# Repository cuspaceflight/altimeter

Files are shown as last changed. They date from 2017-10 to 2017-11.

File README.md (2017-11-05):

# CUSF Altimeter
### This project is a barebones altimeter for use in the freshers rocket challenge. The below instructions are specific to Linux systems only.

## Setting up the Repositiory

1. Setup the repository using the following commands:
```
$ git clone https://github.com/cuspaceflight/altimeter.git
$ cd altimeter
$ git submodule update --init
$ cd ChibiOS
$ git checkout stable_16.1.x
```
2. To succesfully compile firmware you will need to install gcc:
```
$ sudo apt-get install gcc-arm-none-eabi
```
3. Test the installation by compiling the firmware template:
```
$ cd ../firmware
$ make
```

## Analysing Log Files

1. Copy the file "log_0000x.bin" you wish to decode into the altimeter/logs directory

2. From the terminal run:
```
$ python3 log_file_parser.py log_0000x.bin
```

The output will print directly to the terminal window.

## Making Firmware Changes

This will be explained in depth in the sessions, however the files which you will want to modify (status.c, measurements.c and logging.c) can be found in the altimeter/firmware directory.

Compile using the command:
``` 
$ make
```
If successful something similar to the below should appear in the terminal window:

```
...
Compiling testbmk.c
Compiling main.c
Compiling ms5611.c
Compiling measure.c
Compiling status.c
Compiling microsd.c
Compiling logging.c
Linking build/altimeter.elf
Creating build/altimeter.bin
Creating build/altimeter.hex
Creating build/altimeter.dmp
Creating build/altimeter.list

   text	   data	    bss	    dec	    hex	filename
  43900	   8896	 122628	 175424	  2ad40	build/altimeter.elf

Done
```

### References

ChibiOs - http://www.chibios.org/dokuwiki/doku.php?id=chibios:documentation:start

GDB - https://github.com/blacksphere/blackmagic/wiki/Useful-GDB-commands

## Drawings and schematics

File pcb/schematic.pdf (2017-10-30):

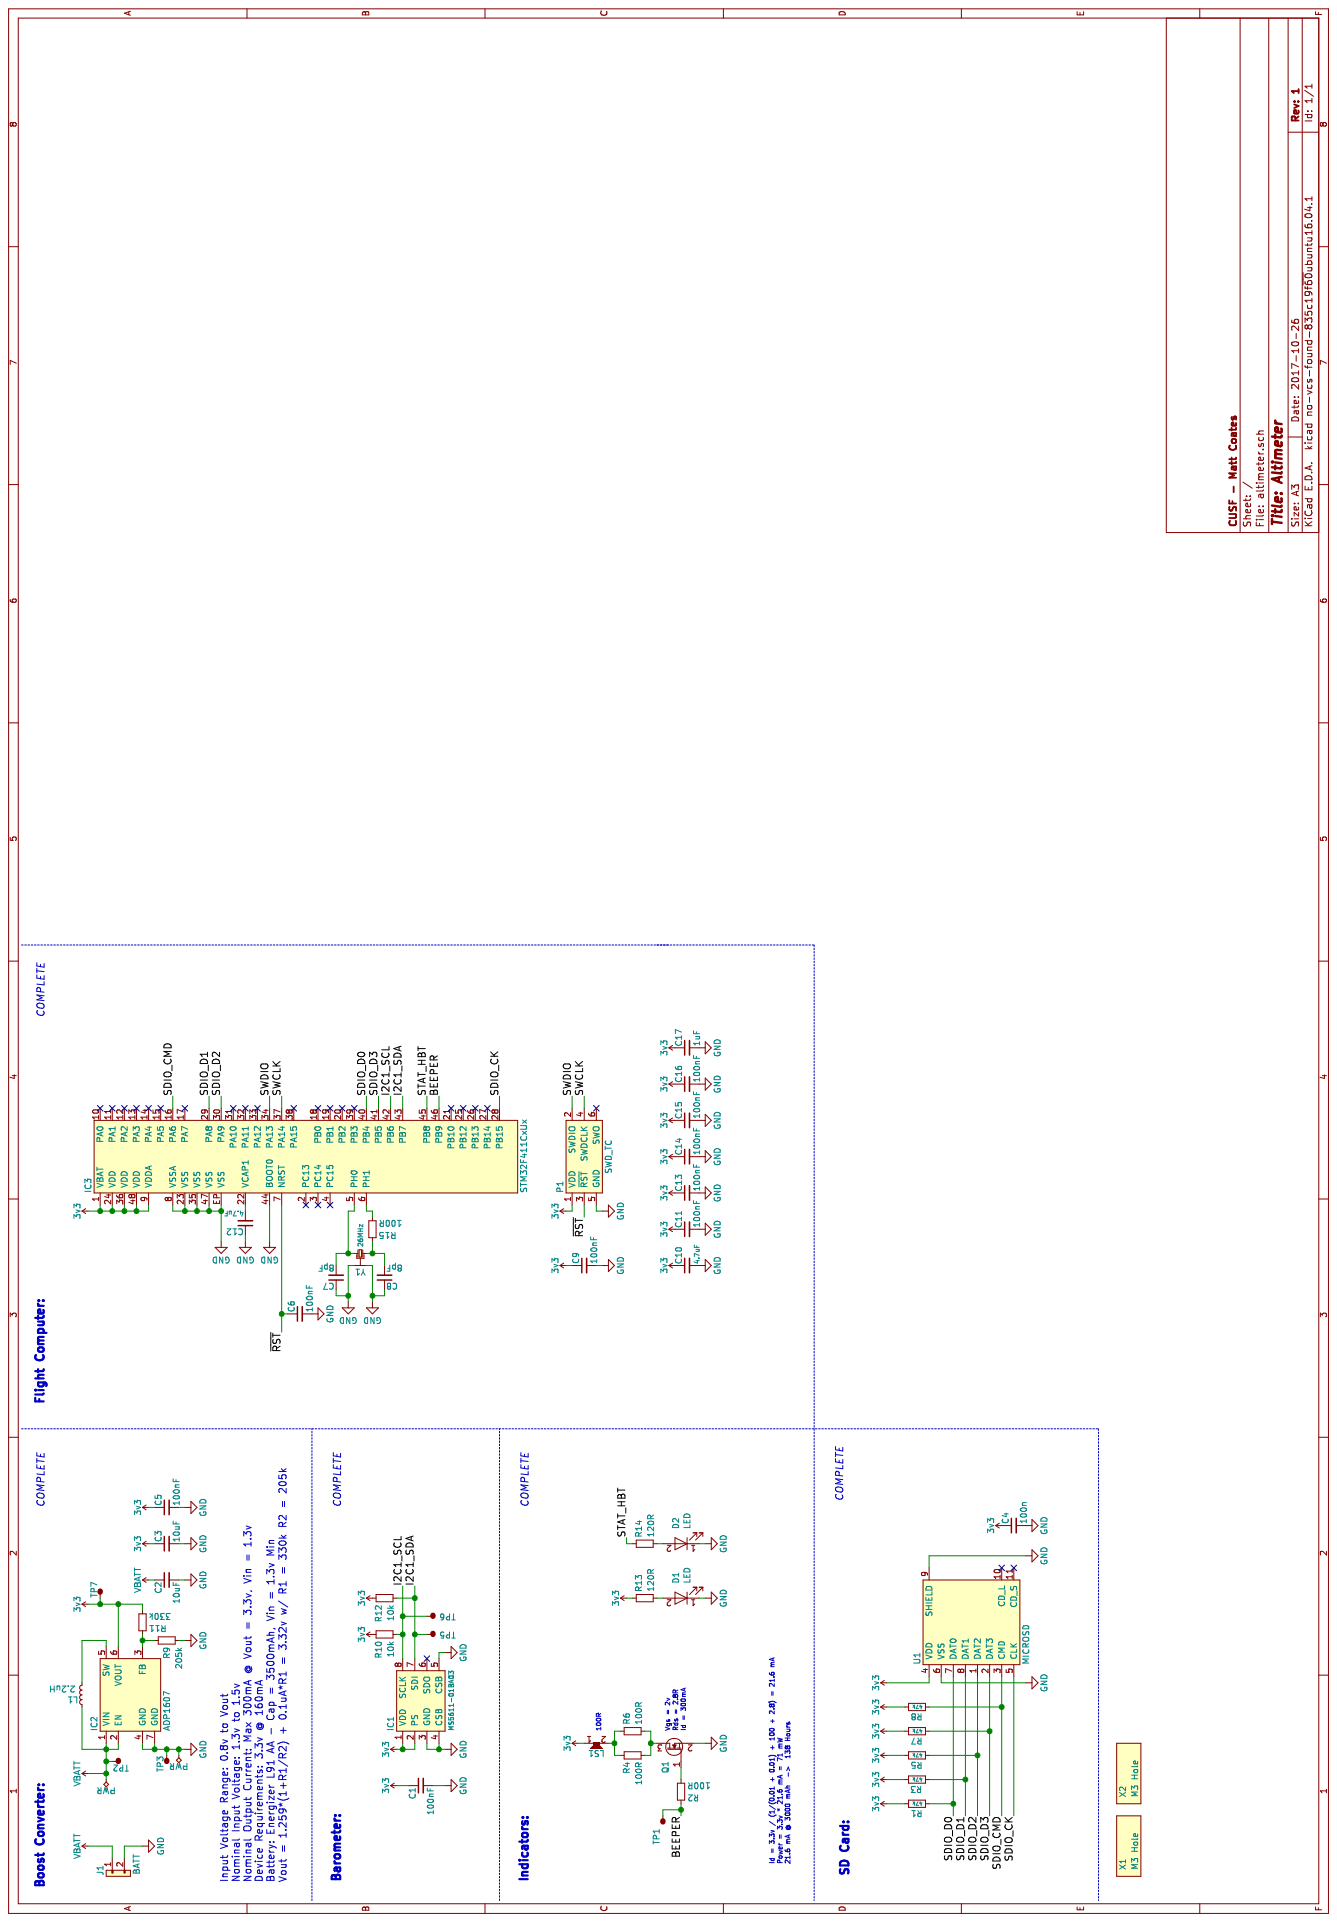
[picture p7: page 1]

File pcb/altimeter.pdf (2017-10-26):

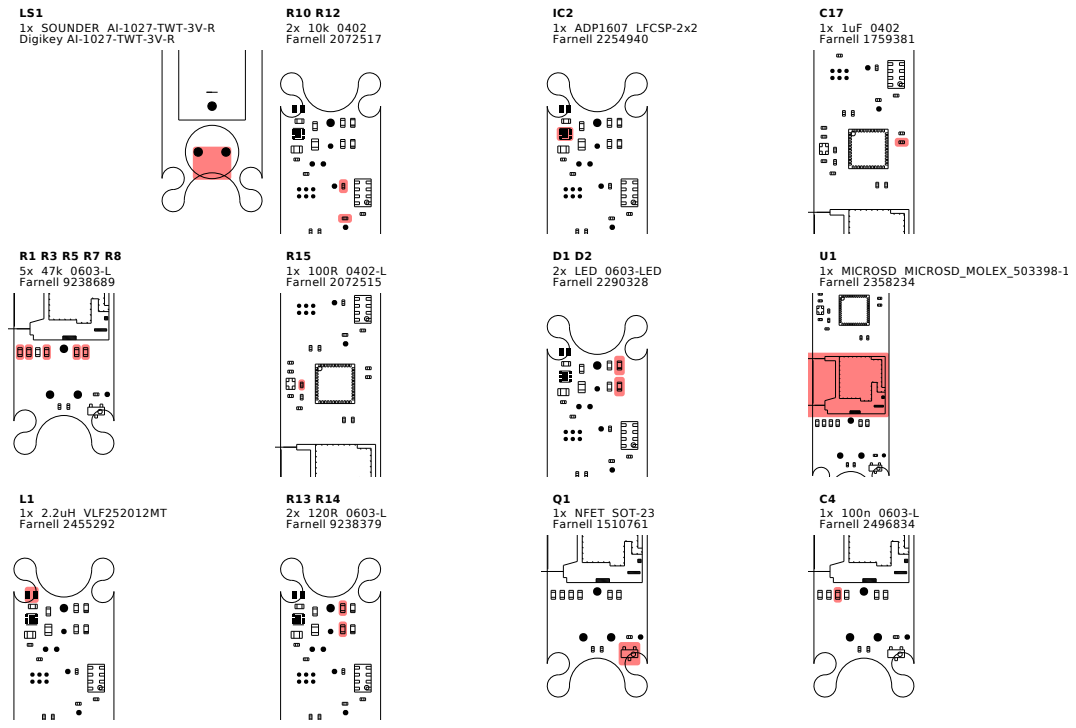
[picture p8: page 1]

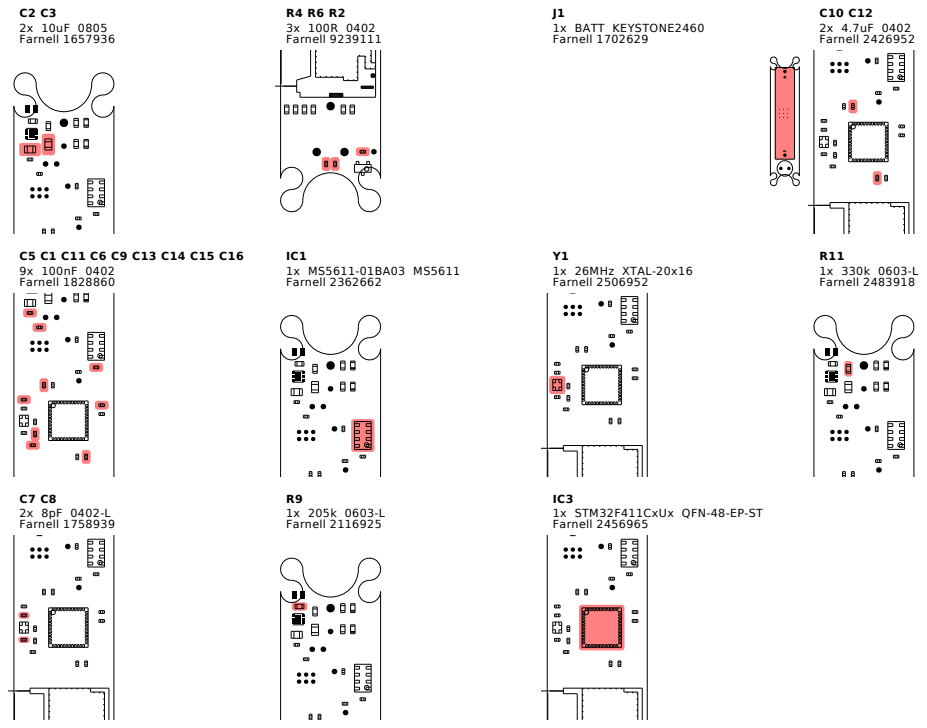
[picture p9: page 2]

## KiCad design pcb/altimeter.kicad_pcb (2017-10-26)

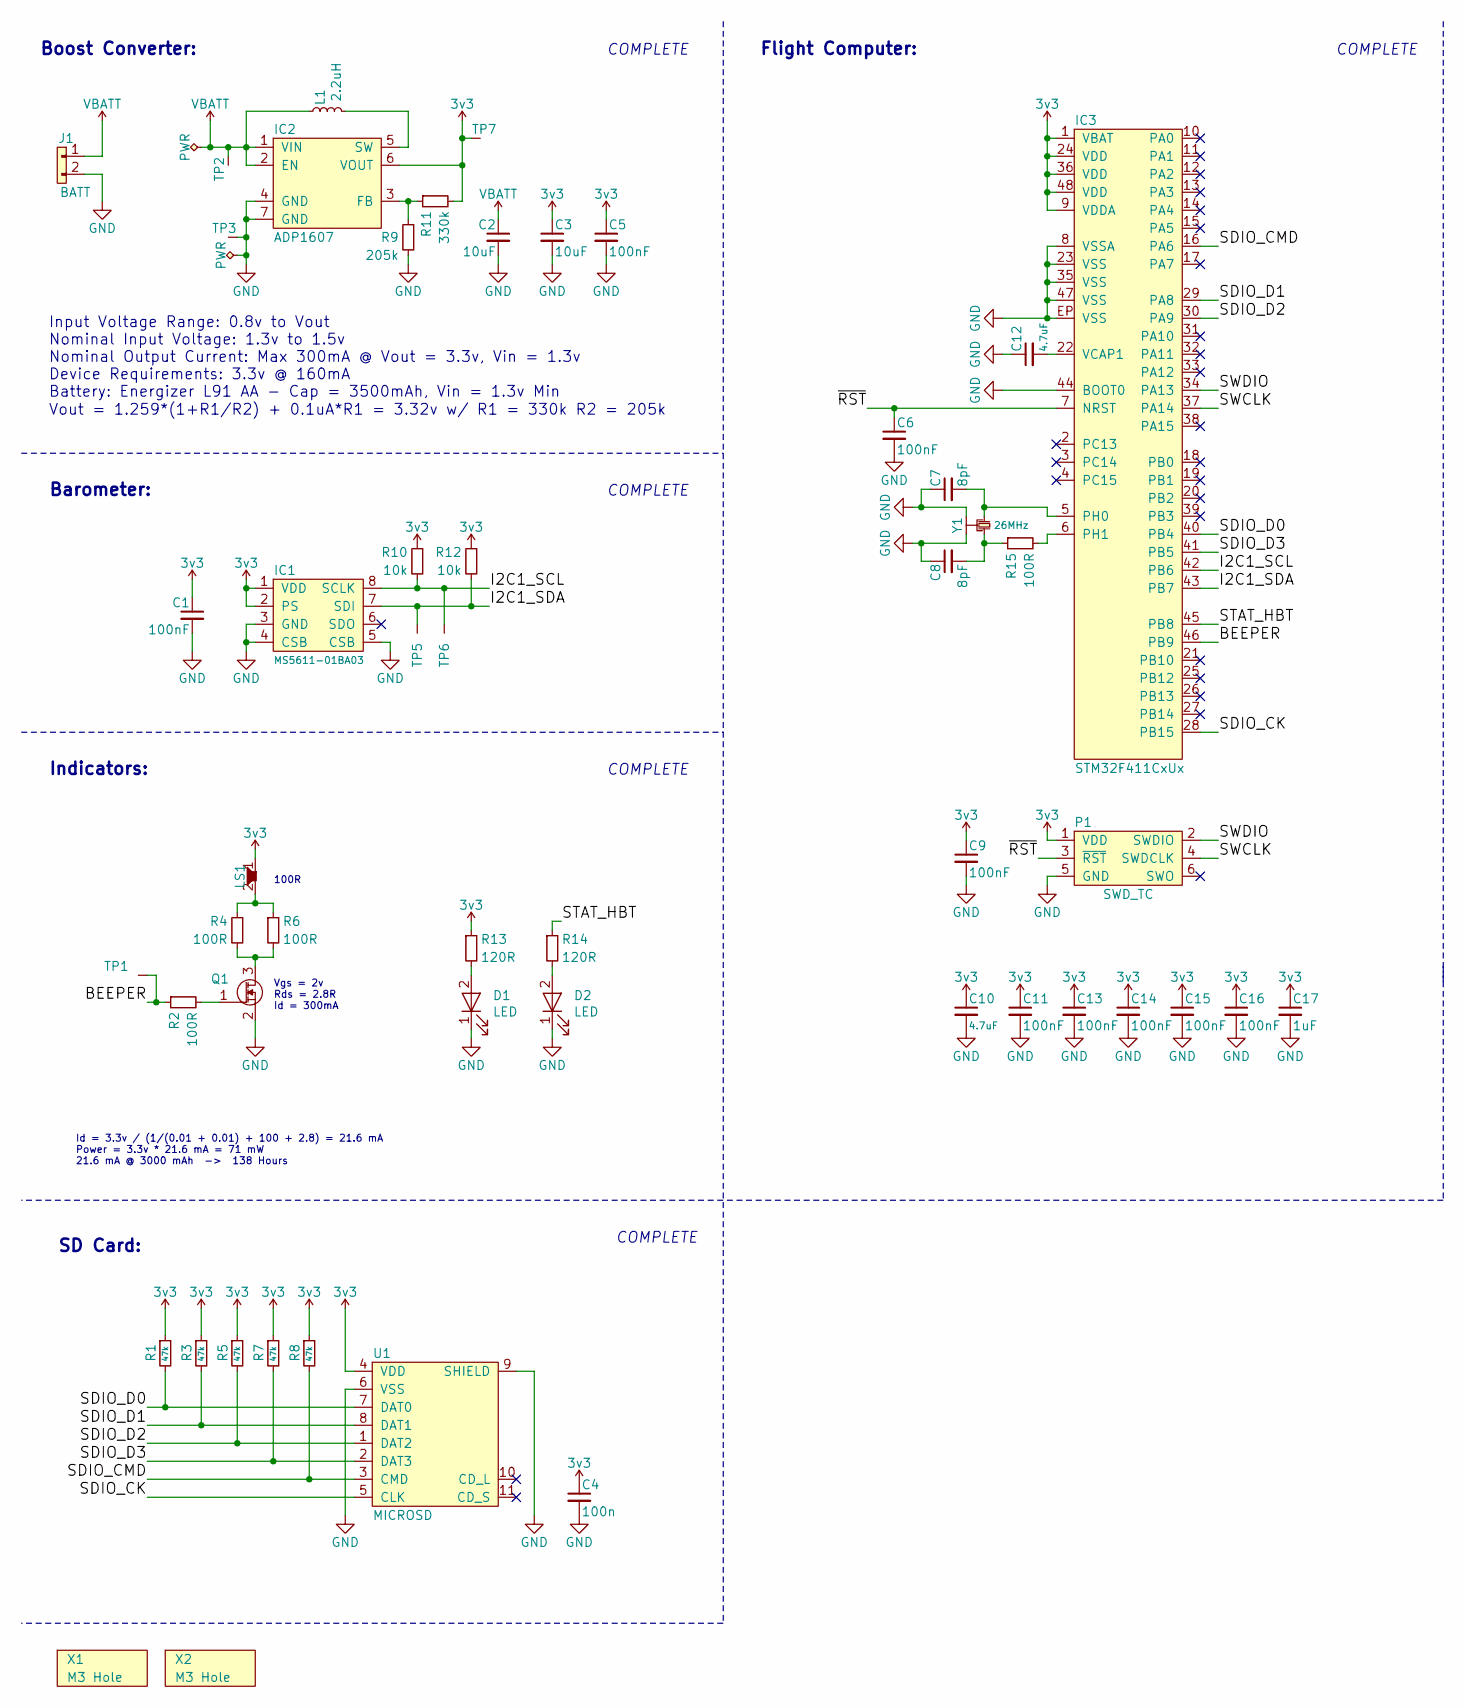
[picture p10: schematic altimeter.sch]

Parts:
C1, C5, C6, C9, C11, C13, C14, C15, C16: 100nF; 0402; Farnell 1828860
C2, C3: 10uF; 0805; Farnell 1657936
C4: 100n; 0603-L; Farnell 2496834
C7, C8: 8pF; 0402-L; Farnell 1758939
C10, C12: 4.7uF; 0402; Farnell 2426952
C17: 1uF; 0402; Farnell 1759381
D1, D2: LED; 0603-LED; Farnell 2290328
IC1: MS5611-01BA03; MS5611; Farnell 2362662
IC2: ADP1607; LFCSP-2x2; Farnell 2254940
IC3: STM32F411CxUx; QFN-48-EP-ST; Farnell 2456965
J1: BATT; KEYSTONE2460; Farnell 1702629
L1: 2.2uH; VLF252012MT; Farnell 2455292
LS1: SOUNDER; AI-1027-TWT-3V-R; Digikey AI-1027-TWT-3V-R
P1: SWD_TC; TC2030-NL
Q1: NFET; SOT-23; Farnell 1510761
R1, R3, R5, R7, R8: 47k; 0603-L; Farnell 9238689
R2, R4, R6: 100R; 0402; Farnell 9239111
R9: 205k; 0603-L; Farnell 2116925
R10, R12: 10k; 0402; Farnell 2072517
R11: 330k; 0603-L; Farnell 2483918
R13, R14: 120R; 0603-L; Farnell 9238379
R15: 100R; 0402-L; Farnell 2072515
TP1, TP2, TP3, TP5, TP6, TP7: TESTPAD
U1: MICROSD; MICROSD_MOLEX_503398-1892; Farnell 2358234
X1, X2: M3 Hole; M3_MOUNT
Y1: 26MHz; XTAL-20x16; Farnell 2506952

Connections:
3v3: C1.1, C3.1, C4.1, C5.1, C9.1, C10.1, C11.1, C13.1, C14.1, C15.1, C16.1, C17.1, IC1.1 (VDD), IC1.2 (PS), IC2.6 (VOUT), IC3.1 (VBAT), IC3.9 (VDDA), IC3.24 (VDD), IC3.36 (VDD), IC3.48 (VDD), LS1.1, P1.1 (VDD), R1.1, R3.1, R5.1, R7.1, R8.1, R10.1, R11.2, R12.1, R13.1, TP7.1, U1.4 (VDD)
/BEEPER: IC3.46 (PB9), R2.1, TP1.1
/I2C1_SCL: IC1.8 (SCLK), IC3.42 (PB6), R10.2, TP6.1
/I2C1_SDA: IC1.7 (SDI), IC3.43 (PB7), R12.2, TP5.1
/SDIO_CK: IC3.28 (PB15), U1.5 (CLK)
/SDIO_CMD: IC3.16 (PA6), R8.2, U1.3 (CMD)
/SDIO_D0: IC3.40 (PB4), R1.2, U1.7 (DAT0)
/SDIO_D1: IC3.29 (PA8), R3.2, U1.8 (DAT1)
/SDIO_D2: IC3.30 (PA9), R5.2, U1.1 (DAT2)
/SDIO_D3: IC3.41 (PB5), R7.2, U1.2 (DAT3)
/STAT_HBT: IC3.45 (PB8), R14.1
/SWCLK: IC3.37 (PA14), P1.4 (SWDCLK)
/SWDIO: IC3.34 (PA13), P1.2 (SWDIO)
/~RST: C6.1, IC3.7 (NRST), P1.3 (~RST)
GND: C1.2, C2.2, C3.2, C4.2, C5.2, C6.2, C7.1, C8.1, C9.2, C10.2, C11.2, C12.1, C13.2, C14.2, C15.2, C16.2, C17.2, D1.1 (K), D2.1 (K), IC1.3 (GND), IC1.4 (CSB), IC1.5 (CSB), IC2.4 (GND), IC2.7 (GND), IC3.8 (VSSA), IC3.23 (VSS), IC3.35 (VSS), IC3.44 (BOOT0), IC3.47 (VSS), IC3.EP (VSS), J1.2, P1.5 (GND), Q1.2 (S), R9.2, TP3.1, U1.6 (VSS), U1.9 (SHIELD), Y1.2, Y1.4
unnamed: C7.2, IC3.5 (PH0), Y1.1
unnamed: C8.2, R15.1, Y1.3
unnamed: C12.2, IC3.22 (VCAP1)
unnamed: D1.2 (A), R13.2
unnamed: D2.2 (A), R14.2
unnamed: IC2.3 (FB), R9.1, R11.1
unnamed: IC2.5 (SW), L1.2
unnamed: IC3.6 (PH1), R15.2
unnamed: LS1.2, R4.1, R6.1
unnamed: Q1.1 (G), R2.2
unnamed: Q1.3 (D), R4.2, R6.2
VBATT: C2.1, IC2.1 (VIN), IC2.2 (EN), J1.1, L1.1, TP2.1

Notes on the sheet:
Boost Converter:
Input Voltage Range: 0.8v to Vout Nominal Input Voltage: 1.3v to 1.5v Nominal Output Current: Max 300mA @ Vout = 3.3v, Vin = 1.3v Device Requirements: 3.3v @ 160mA Battery: Energizer L91 AA - Cap = 3500mAh, Vin = 1.3v Min
Vout = 1.259*(1+R1/R2) + 0.1uA*R1 = 3.32v w/ R1 = 330k R2 = 205k
Barometer:
Indicators:
100R
Id = 3.3v / (1/(0.01 + 0.01) + 100 + 2.8) = 21.6 mA Power = 3.3v * 21.6 mA = 71 mW 21.6 mA @ 3000 mAh -> 138 Hours
Vgs = 2v Rds = 2.8R Id = 300mA
Flight Computer:
SD Card:
COMPLETE

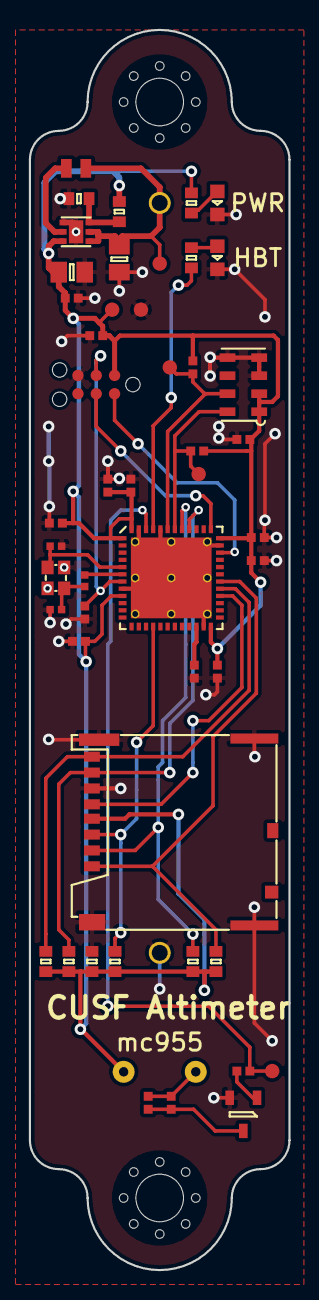
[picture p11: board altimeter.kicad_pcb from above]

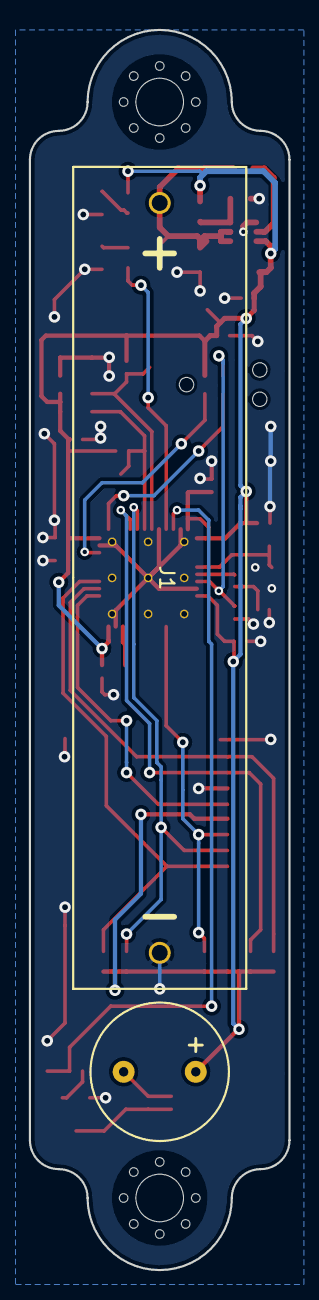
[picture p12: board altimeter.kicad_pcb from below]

Board: 2 copper layers, 18.0 x 86.0 mm, 52 parts (2 on the bottom side), 27 nets.

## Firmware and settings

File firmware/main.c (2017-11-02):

#include "ch.h"
#include "hal.h"
#include "measure.h"
#include "status.h"
#include "logging.h"

/* Application Entry Point */
int main(void){

    /* Allow debug access during WFI sleep */
    DBGMCU->CR |= DBGMCU_CR_DBG_SLEEP;

    /* Initialise ChibiOS */
    halInit();
    chSysInit();
    
    /* Start Status Monitor */
    begin_status();
    
    /* Start Datalogger */
    logging_init();

    /* Start Measurement Handler*/
    begin_measurements();

    /* Do Nothing */
    while (true) {
    }
}

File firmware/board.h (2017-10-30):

/*
    ChibiOS - Copyright (C) 2006..2016 Giovanni Di Sirio
    Licensed under the Apache License, Version 2.0 (the "License");
    you may not use this file except in compliance with the License.
    You may obtain a copy of the License at
    http://www.apache.org/licenses/LICENSE-2.0
    Unless required by applicable law or agreed to in writing, software
    distributed under the License is distributed on an "AS IS" BASIS,
    WITHOUT WARRANTIES OR CONDITIONS OF ANY KIND, either express or implied.
    See the License for the specific language governing permissions and
    limitations under the License.
*/

/*
    Generated by gen-board.h.py based on board.yaml
*/

#ifndef _BOARD_H_
#define _BOARD_H_


/*
    Setup for Altimeter
*/

/*
    Board identifier
*/
#define BOARD_ALTIMETER
#define BOARD_NAME                     "Altimeter"

/*
    Board oscillators-related settings.
*/
#if !defined(STM32_LSECLK)
#define STM32_LSECLK                   0U
#endif

#if !defined(STM32_HSECLK)
#define STM32_HSECLK                   26000000U
#endif

/*
    Board voltages
    Required for performance limits calculation.
*/
#define STM32_VDD                      330U

/*
    MCU type as defined in the ST header.
*/
#define STM32F411xE

/*
    IO pins assignments.
*/
#define GPIOA_PIN0                     0U
#define GPIOA_PIN1                     1U
#define GPIOA_PIN2                     2U
#define GPIOA_PIN3                     3U
#define GPIOA_PIN4                     4U
#define GPIOA_PIN5                     5U
#define GPIOA_SDIO_CMD                 6U
#define GPIOA_PIN7                     7U
#define GPIOA_SDIO_D1                  8U
#define GPIOA_SDIO_D2                  9U
#define GPIOA_PIN10                    10U
#define GPIOA_PIN11                    11U
#define GPIOA_PIN12                    12U
#define GPIOA_SWDIO                    13U
#define GPIOA_SWCLK                    14U
#define GPIOA_PIN15                    15U

#define GPIOB_PIN0                     0U
#define GPIOB_PIN1                     1U
#define GPIOB_PIN2                     2U
#define GPIOB_PIN3                     3U
#define GPIOB_SDIO_DO                  4U
#define GPIOB_SDIO_D3                  5U
#define GPIOB_I2C1_SCL                 6U
#define GPIOB_I2C1_SDA                 7U
#define GPIOB_STAT                     8U
#define GPIOB_BEEP                     9U
#define GPIOB_PIN10                    10U
#define GPIOB_PIN11                    11U
#define GPIOB_PIN12                    12U
#define GPIOB_PIN13                    13U
#define GPIOB_PIN14                    14U
#define GPIOB_SDIO_CK                  15U

#define GPIOC_PIN0                     0U
#define GPIOC_PIN1                     1U
#define GPIOC_PIN2                     2U
#define GPIOC_PIN3                     3U
#define GPIOC_PIN4                     4U
#define GPIOC_PIN5                     5U
#define GPIOC_PIN6                     6U
#define GPIOC_PIN7                     7U
#define GPIOC_PIN8                     8U
#define GPIOC_PIN9                     9U
#define GPIOC_PIN10                    10U
#define GPIOC_PIN11                    11U
#define GPIOC_PIN12                    12U
#define GPIOC_PIN13                    13U
#define GPIOC_PIN14                    14U
#define GPIOC_PIN15                    15U

#define GPIOD_PIN0                     0U
#define GPIOD_PIN1                     1U
#define GPIOD_PIN2                     2U
#define GPIOD_PIN3                     3U
#define GPIOD_PIN4                     4U
#define GPIOD_PIN5                     5U
#define GPIOD_PIN6                     6U
#define GPIOD_PIN7                     7U
#define GPIOD_PIN8                     8U
#define GPIOD_PIN9                     9U
#define GPIOD_PIN10                    10U
#define GPIOD_PIN11                    11U
#define GPIOD_PIN12                    12U
#define GPIOD_PIN13                    13U
#define GPIOD_PIN14                    14U
#define GPIOD_PIN15                    15U

#define GPIOE_PIN0                     0U
#define GPIOE_PIN1                     1U
#define GPIOE_PIN2                     2U
#define GPIOE_PIN3                     3U
#define GPIOE_PIN4                     4U
#define GPIOE_PIN5                     5U
#define GPIOE_PIN6                     6U
#define GPIOE_PIN7                     7U
#define GPIOE_PIN8                     8U
#define GPIOE_PIN9                     9U
#define GPIOE_PIN10                    10U
#define GPIOE_PIN11                    11U
#define GPIOE_PIN12                    12U
#define GPIOE_PIN13                    13U
#define GPIOE_PIN14                    14U
#define GPIOE_PIN15                    15U
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

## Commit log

2017-10-11 schematic complete
    [altimeter.kicad_pcb, altimeter.sch]
2017-10-12 created board outline and placed components
    [altimeter.sch]
2017-10-14 finished board
    [altimeter-B.Cu.gbl, altimeter-B.Mask.gbs, altimeter-B.Paste.gbp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]
2017-10-26 added panel and updated bom
    [altimeter-B.Cu.gbl, altimeter-B.Mask.gbs, altimeter-B.Paste.gbp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]
2017-10-30 reorganised folder
    [altimeter-B.Cu.gbl, altimeter-B.Mask.gbs, altimeter-B.SilkS.gbo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]
2017-10-30 added microsd driver and compiled fatfs
2019-05-07 added plotting, need to implement filtering
2019-05-09 added filtering and subplots!
2019-05-11 added ground level pressure
2019-05-12 flight data added
    [escott_stratologger.csv]
